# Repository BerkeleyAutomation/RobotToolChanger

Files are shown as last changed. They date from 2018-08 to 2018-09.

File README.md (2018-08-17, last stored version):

# Tool changer for robots
In this work we developed a tool changer for robots. 
With minor adjustments the tool changer design can be retrofit to most mobile and stationary robots.
The project includes the design, manufacture, programing, and evaluation of a tool changer for robots. 
To examine the design we evaluated the tool changer on ABB YUMI, two-arm stationary robot. 

## Getting Started
This work was first published at [CASE-2018](/http://ronberenstein.com/publications.html). 
This publication present the three main components needed to create a tool changer, robot, tool, and tool housing.
Most of the component were 3D printed which may contributes to the adoption of the design.

## The tools
For this case study we created 4 tools, camera, light, cutting, and moister sensor tool. 
For each tool we provide the CAD design, the electrical drawing, and the program to control it.

A [raspberryPi zero w](https://www.raspberrypi.org/products/raspberry-pi-zero-w/) is installed in each tool and is used as the main computing unit of the tool. 
The connection of the tool with the remote computer is via WIFI. The robot should provide power (24v) to the tool.

### preparing the raspberryPi
Before starting using the raspberryPi please follow the instructions [here](/https://projects.raspberrypi.org/en/projects/raspberry-pi-setting-up). 
In this work we will use the NOOBS installer with **Raspbian**.

After Raspbian is installed we will need to add the main program and the [reset button program](/https://github.com/BerkeleyAutomation/RobotToolChanger/blob/master/rebootUsingButton.py)
to the raspberryPi autostart using crontab ([tip](/https://raspberrypi.stackexchange.com/questions/8734/execute-script-on-start-up)).

The tool and the remote computer **must** be connected to the same router, and are able to communicate (check using ping).
Make sure the same network is used when the raspberryPi starts ([tip](/https://raspi.tv/2017/how-to-auto-connect-your-raspberry-pi-to-a-hidden-ssid-wifi-network)).

## points to include
* add examples
```
Give the example
```
## Built With

* [Dropwizard](http://www.dropwizard.io/1.0.2/docs/) - The web framework used
* [Maven](https://maven.apache.org/) - Dependency Management
* [ROME](https://rometools.github.io/rome/) - Used to generate RSS Feeds

## Contributing

Please read [CONTRIBUTING.md](https://gist.github.com/PurpleBooth/b24679402957c63ec426) for details on our code of conduct, and the process for submitting pull requests to us.

## Versioning

We use [SemVer](http://semver.org/) for versioning. For the versions available, see the [tags on this repository](https://github.com/your/project/tags). 

## Authors

* **Billie Thompson** - *Initial work* - [PurpleBooth](https://github.com/PurpleBooth)

See also the list of [contributors](https://github.com/your/project/contributors) who participated in this project.

## License

This project is licensed under the MIT License - see the [LICENSE.md](LICENSE.md) file for details

## Acknowledgments

* Hat tip to anyone whose code was used
* Inspiration
* etc

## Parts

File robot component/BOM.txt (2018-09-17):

Part			Quantity		Price		Comments and URLs
--------------------------------------------------------------------------------------------------------------
4mm bolt (flat head)	12					L=16mm, https://www.mcmaster.com/92855a416
4mm bolt (flat head)	12					L=8mm, https://www.mcmaster.com/92855a408
4mm nut (nylock)	18					https://www.mcmaster.com/94205a230
3mm bolt 		2					L-60mm, https://www.mcmaster.com/91290A181
3mm insert		1					L=6mm
3mm bolt 		1					L=8mm
90 Degree Angle							https://www.mcmaster.com/8982k56
6061 Aluminum plate	1			45$		https://www.mcmaster.com/8975K142

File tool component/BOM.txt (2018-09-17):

Part			Quantity		Price		Comments and URLs
--------------------------------------------------------------------------------------------------------------
Spring			2					inner diameter => 8mm, L=~15mm
Tension bolt		2					self manufactured
Magnets			4			~15$		5x5mm, https://www.amazon.com/gp/product/B07CBN7SF5/ref=oh_aui_search_detailpage?ie=UTF8&psc=1
Spring pin		2					diameter = 4mm
Bearing			2					in D = 4, out D = 8, W = 3
connector		1			~3$		https://www.mouser.com/datasheet/2/273/858-10-003-30-012000-1149118.pdf
External retaining ring	2					for 8mm shaft

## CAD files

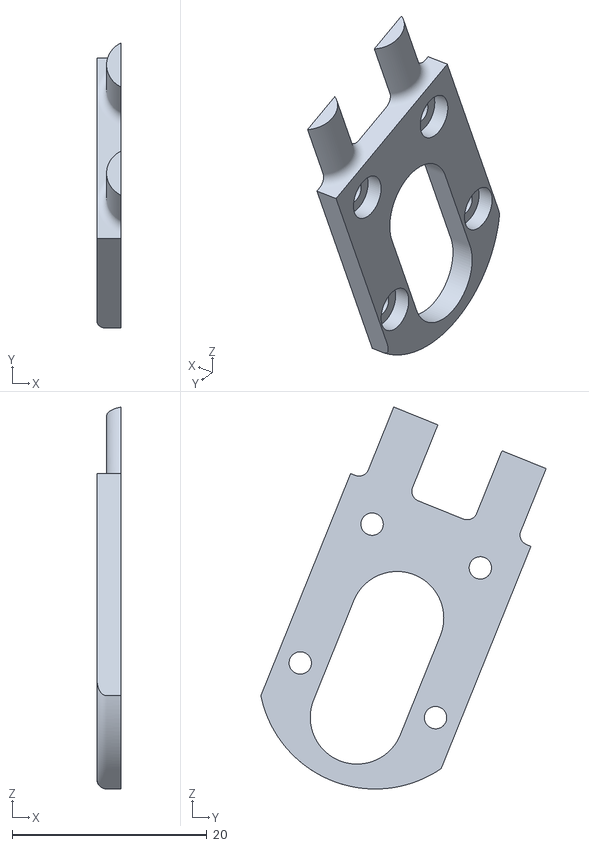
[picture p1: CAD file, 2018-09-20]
robot component/STL/tool-changer main - locking blades-1 Part2-2.STL
2.50 x 29.3 x 39.3

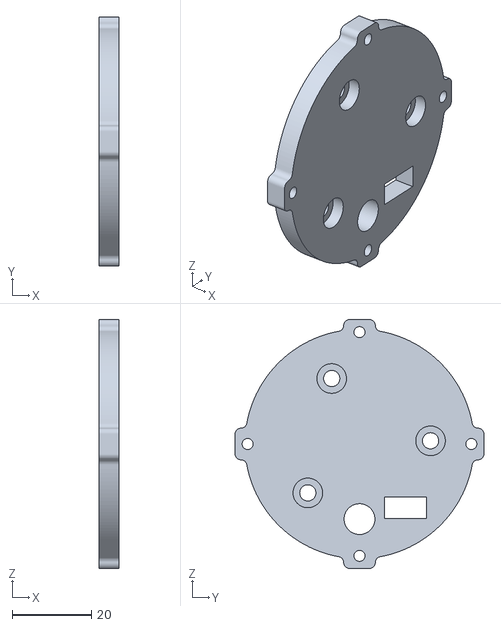
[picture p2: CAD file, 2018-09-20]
robot component/STL/tool-changer main - YUMI plate-2.STL
5.00 x 63.0 x 63.0

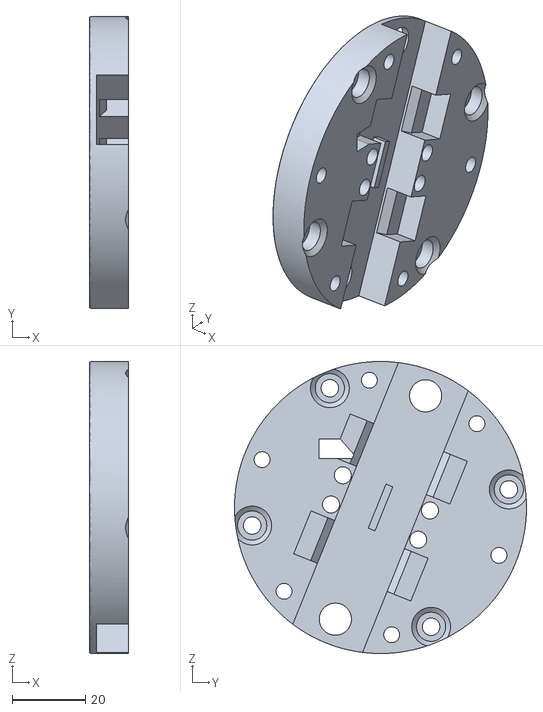
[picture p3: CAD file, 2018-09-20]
robot component/STL/tool-changer main - mid-1.STL
10.7 x 80.0 x 80.0

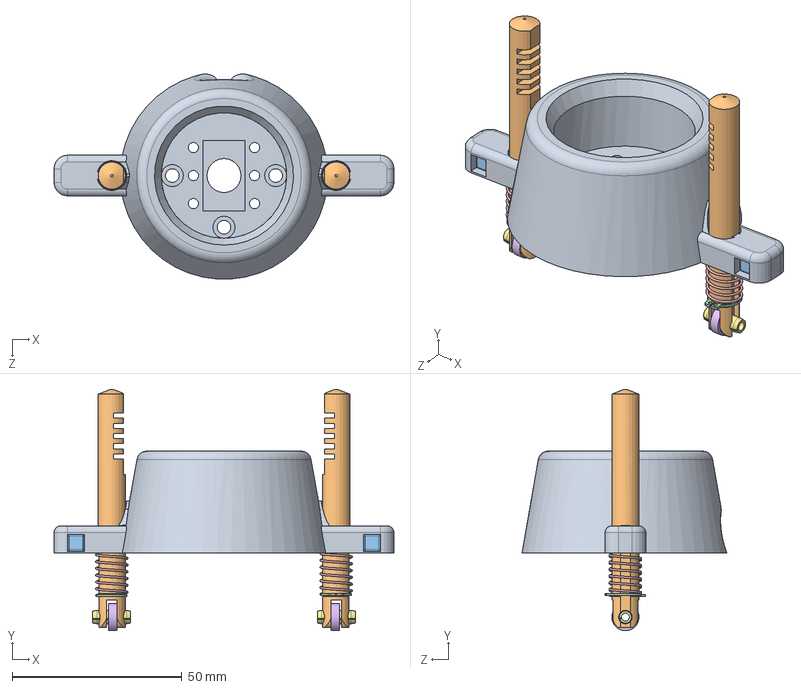
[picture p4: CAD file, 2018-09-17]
tool component/CAD/tool component assem.SLDASM
100.0 x 71.0 x 60.3 mm
tool component
tension bolt 2.1 x 2
5mm magnet x 4
basic external retaining ring_ai x 2
spring for tention bolt x 2
bearing 4-8-3 x 2
spring pin slotted_ai x 2

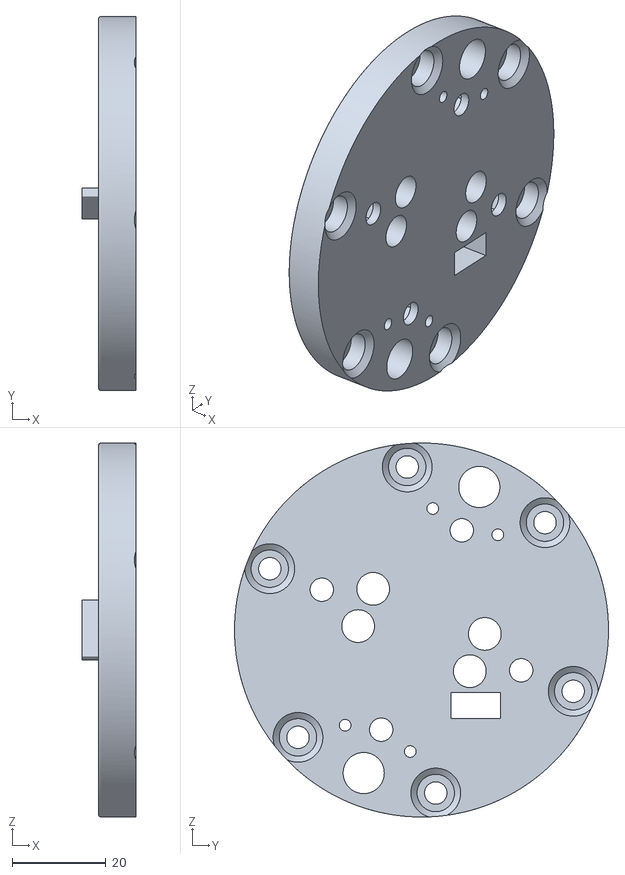
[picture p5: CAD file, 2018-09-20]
robot component/STL/tool-changer main - cap-1.STL
11.5 x 80.0 x 80.0

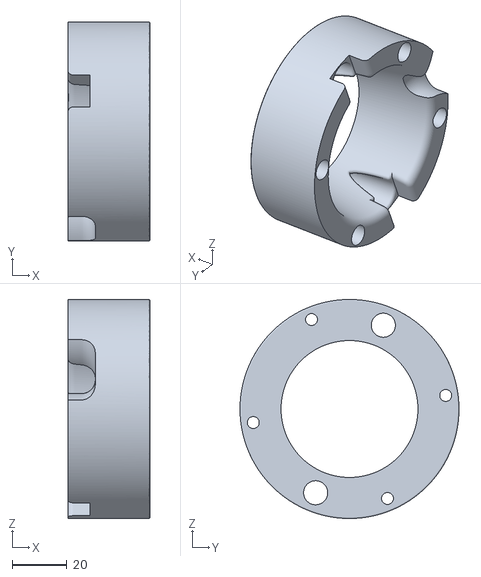
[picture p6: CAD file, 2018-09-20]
robot component/STL/tool-changer main - cone.-1.STL
30.0 x 80.0 x 80.0

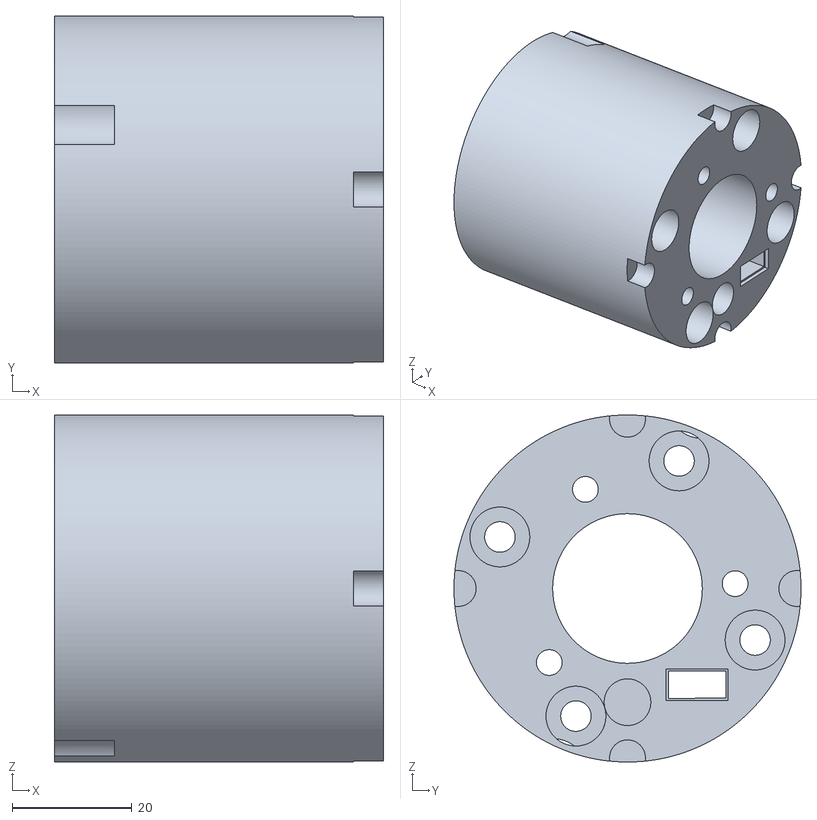
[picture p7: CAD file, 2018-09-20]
robot component/STL/tool-changer main - YUMI adapter-2.STL
55.0 x 58.0 x 58.0

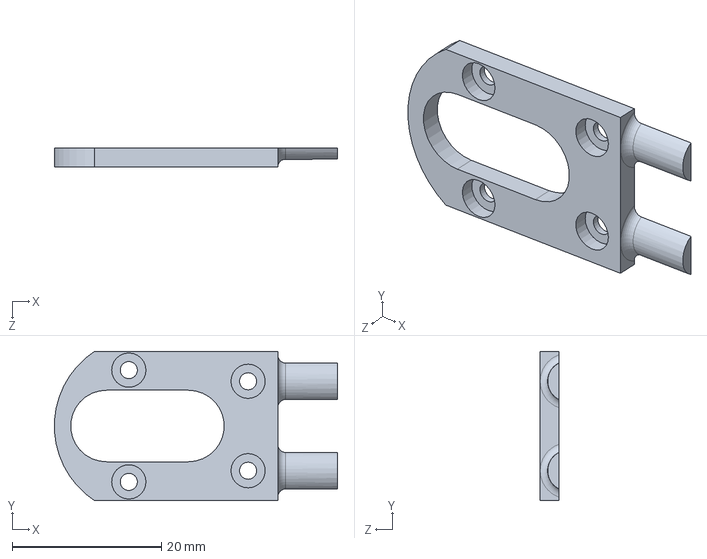
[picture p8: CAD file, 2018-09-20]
robot component/CAD/Part2.SLDPRT
38.0 x 20.0 x 2.50 mm

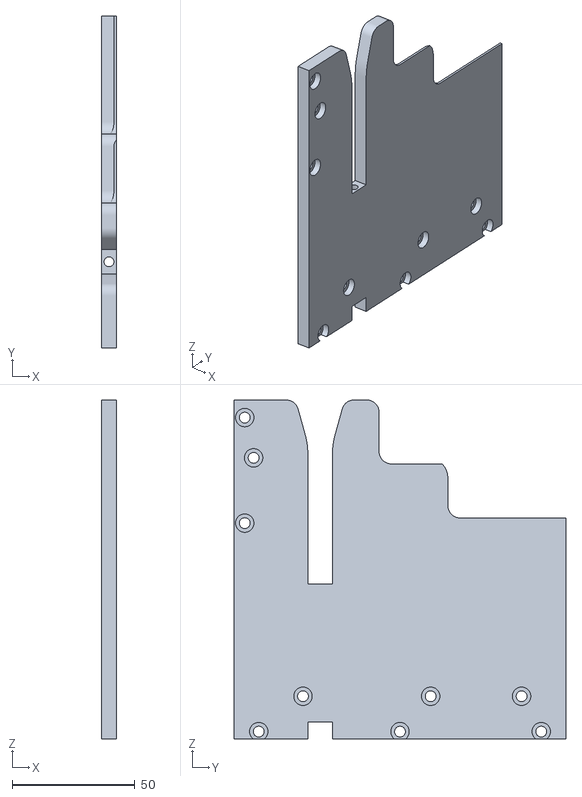
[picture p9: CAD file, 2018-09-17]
tool housing/STL/left-1.STL
6.00 x 135.0 x 138.0

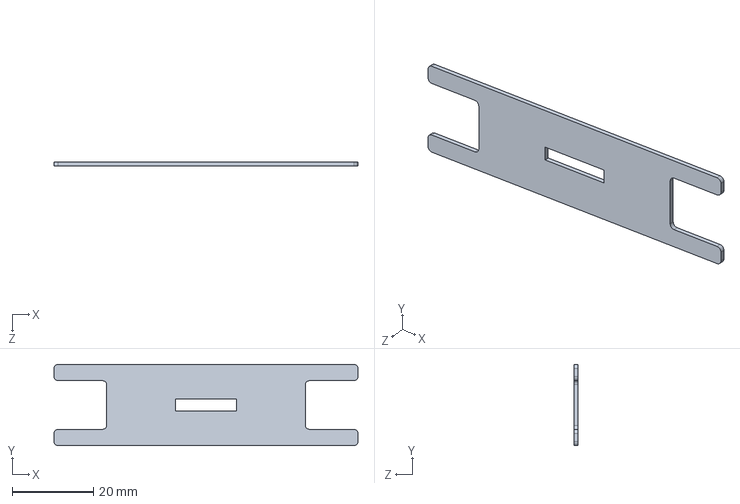
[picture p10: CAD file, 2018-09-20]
robot component/CAD/base plate.SLDPRT
75.0 x 20.0 x 1.00 mm

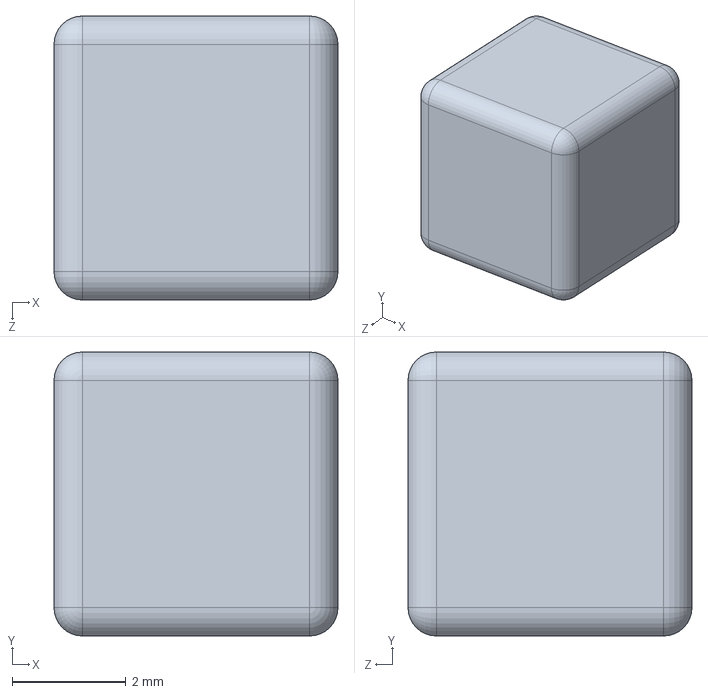
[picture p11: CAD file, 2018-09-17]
tool component/CAD/5mm magnet.SLDPRT
5.00 x 5.00 x 5.00 mm

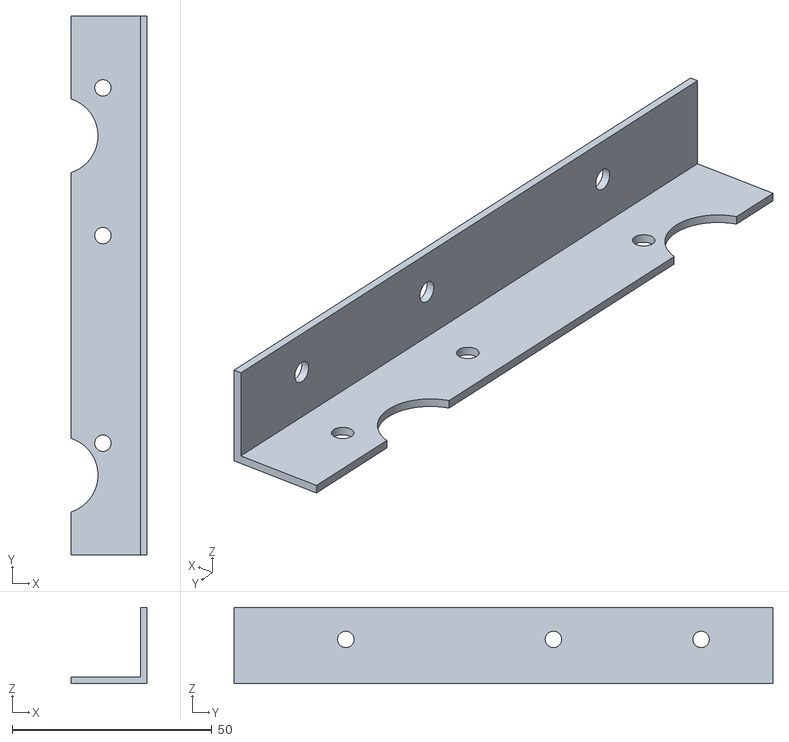
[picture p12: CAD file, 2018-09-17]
tool housing/STL/90deg - left-1.STL
19.1 x 135.0 x 19.0

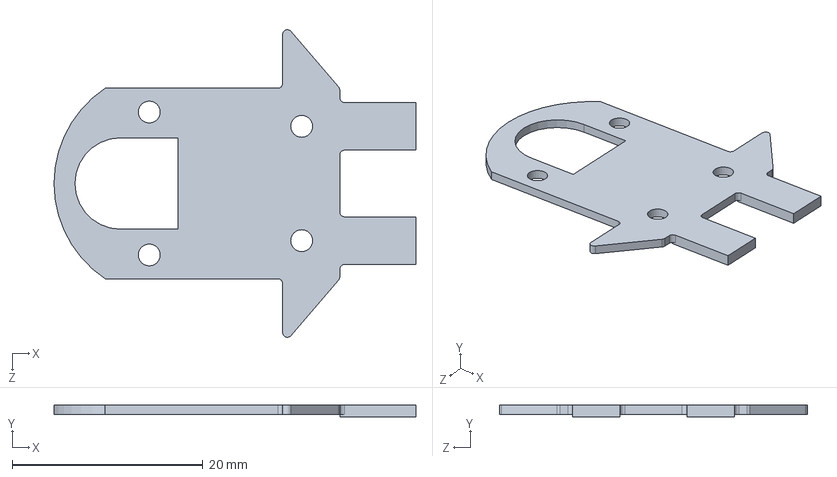
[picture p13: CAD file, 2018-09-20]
robot component/CAD/mid 3.SLDPRT
38.0 x 1.25 x 32.3 mm

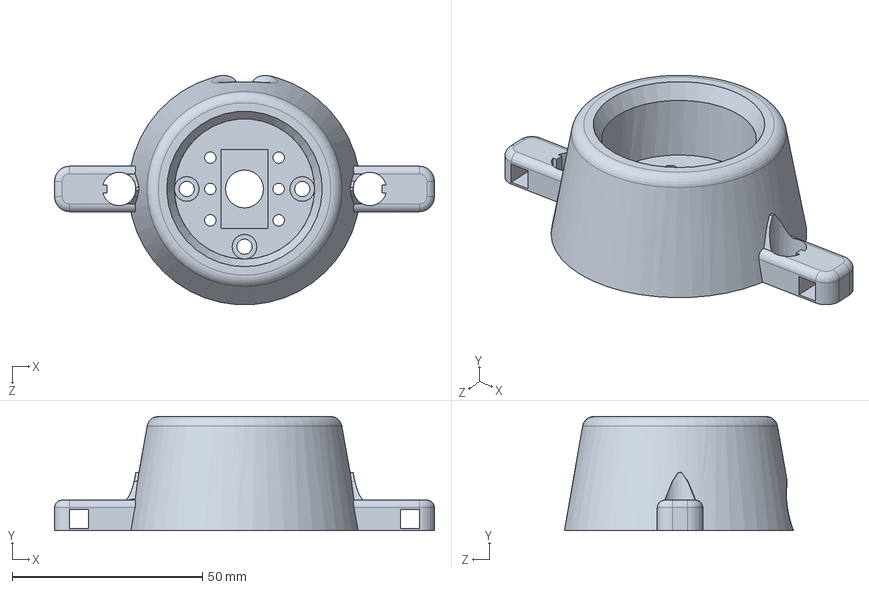
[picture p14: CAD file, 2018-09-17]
tool component/CAD/tool component.SLDPRT
100.0 x 30.0 x 60.3 mm

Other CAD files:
robot component/STL/tool-changer main - locking blades-2 Part2-2.STL
robot component/STL/tool-changer main - locking blades-1 Part2-1.STL
robot component/CAD/mid.SLDPRT
tool housing/STL/90deg - right-2.STL
robot component/CAD/YUMI adapter.SLDPRT
robot component/CAD/YUMI plate.SLDPRT
robot component/CAD/cap.SLDPRT
robot component/CAD/cone..SLDPRT
tool component/CAD/bearing 4-8-3.SLDPRT
tool component/CAD/spring for tention bolt.SLDPRT
tool component/CAD/tension bolt 2.1.SLDPRT
tool housing/STL/back-1.STL
tool housing/STL/right-2.STL
tool housing/STL/slide left-1.STL
tool housing/STL/slide right-1.STL

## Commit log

2018-08-22 adding moisture tool CAD
    [5mm magnet.SLDPRT, CameraTool.SLDASM, Moisture housing backup.SLDPRT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]
2018-08-27 adding moisture sensor electric drawing
2018-09-17 adding files
    [5mm magnet.SLDPRT, 90deg - left-1.STL, 90deg - left.SLDPRT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]
2018-09-20 add parts
    [90deg - left.SLDPRT, 90deg - right.SLDPRT, asm.SLDPRT.SLDASM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]
2018-09-20 update lib
    [Part2.SLDPRT, YUMI adapter.SLDPRT, YUMI plate.SLDPRT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]
